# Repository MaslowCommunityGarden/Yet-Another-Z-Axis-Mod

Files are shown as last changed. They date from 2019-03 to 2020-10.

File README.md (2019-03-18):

# Yet Another Z-Axis Mod

I had gotten the z-axis kit with my Maslow originally, but I frequently found it off of spec when cutting. I tried all the simple fixes (bungee cord, gluing a bushing to the frame to keep alignment), and while they helped, I still had trouble with incomplete cuts way too often.

So I designed my own Z-axis kit that extends the stock solution, but doesn't rely on the Ridgid router's collar and it's not-intended-for-this-purpose mechanics.

The kit relies on the Z-axis motor from the original Maslow z-axis kit. Other than that all parts are 3D printed or listed in the BOM.
 
Additionally you will need the 3D printed parts from the forum and all the materials listed in the BOM.

Shout out to Gary D (@gder) for doing a **lot** of work beta testing and for contributing a bunch of ideas to the design. Thanks to Gary the design is a lot better than it would have been.

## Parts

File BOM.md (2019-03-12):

## Bill of Materials (BOM)

* Wood for the sled. 
* Linear Motion kit (or equivalent). You'll either need a linear-rod kit like <a href="https://smile.amazon.com/gp/product/B0797Q2C92">this one.</a> or equivalent parts. If you decide to source the parts yourself instead, here's what you really need from that kit:
	* 2x 8mm x 150mm smooth rails
	* 1x 8mm x 150mm lead screw
	* 4x LM 8UU bearings (the kit has these embedded inside linear slide blocks, but they pop out easily if you remove the retaining clip)
	* 1x 8mm lead-screw nut
	* 2x 42x24x10mm 8mm rail support block
	* 1x 48x12x27mm 8mm pillow block bearing
	* (You do not need the shaft couplers, plus there is an extra pillow block, and 2 extra rail support blocks)
* One 6mm to 8mm shaft coupler, like <a href="https://smile.amazon.com/gp/product/B06X9W3TNS">this one.</a>
* An assortment of <a href="https://smile.amazon.com/Stainless-Assortment-Precise-Beautiful-Printed/dp/B0714FLXND">M3 screws & nuts.
* Additionally you will need 4 M3x25mm screws
* You will also need some square M3 nuts, as well as some M6 and M8 ones. Probably best to get a kit like <a href="https://smile.amazon.com/gp/product/B06Y3NBT4Z">this one</a>.
* 4x M8 x 30mm hex screws (<a href="https://smile.amazon.com/Machine-Phillips-Threaded-M8-1-25-Threads/dp/B00917MQC8">phillips head</a> or <a href="https://smile.amazon.com/M8-1-25-Socket-Screws-Stainless-Machine/dp/B07GCMGP8S">"button" style</a> [that accepts a hex driver]).
* 2x M8 x 35mm hex screws
* 6x M6 x 35mm (up to 50mm) screws for the motor-assembly cross-braces
* Some M6 x 20mm screws and nuts and M5 x 15mm screws with nuts for mounting parts to the sled
* (Note: I got all of the M8/M6/M5 screws I needed by buying a TV mounting kit like <a href="https://smile.amazon.com/gp/product/B073WKR1QR/ref=oh_aui_search_asin_title?ie=UTF8&psc=1">this one</a>.)

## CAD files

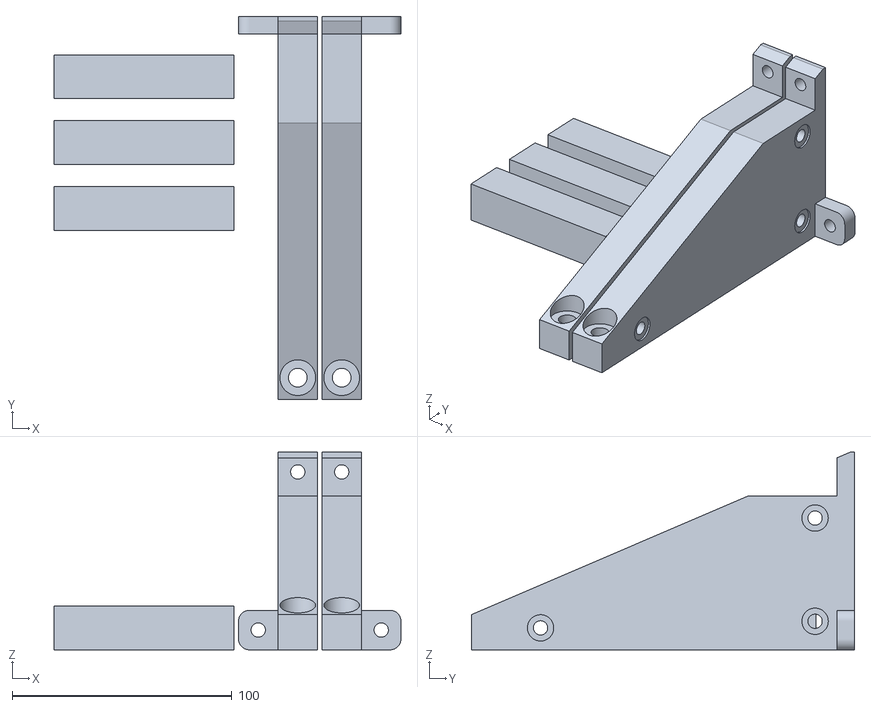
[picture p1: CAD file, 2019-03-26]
Project Files/v3_motor_brace_assembly_all.stl
158.0 x 174.5 x 90.0

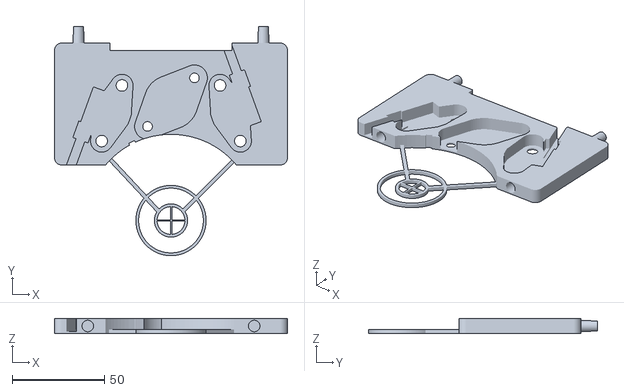
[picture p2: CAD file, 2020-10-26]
Project Files/individual parts (print only if needed)/v3_rods_base_alternate(for larger pillow-block).stl
126.0 x 124.0 x 8.00

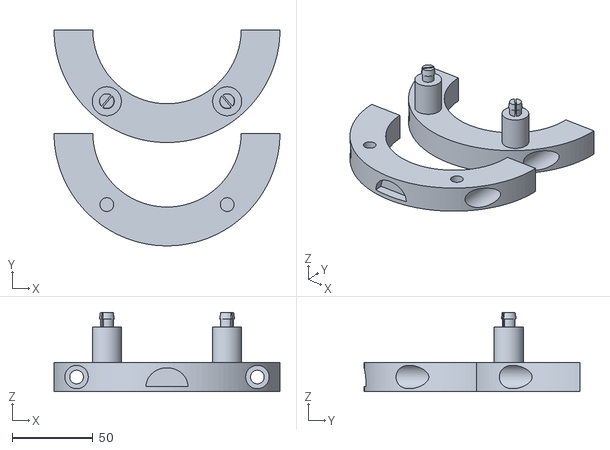
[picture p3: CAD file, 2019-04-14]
Project Files/v3_body_clamp_front_half_braced_pair.stl
140.0 x 133.6 x 49.0

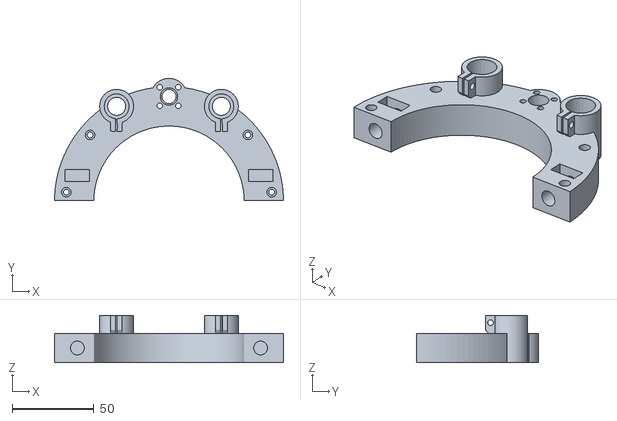
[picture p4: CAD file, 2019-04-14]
Project Files/individual parts (print only if needed)/v3_body_clamp_back_half_bottom_only.stl
140.0 x 74.7 x 29.0

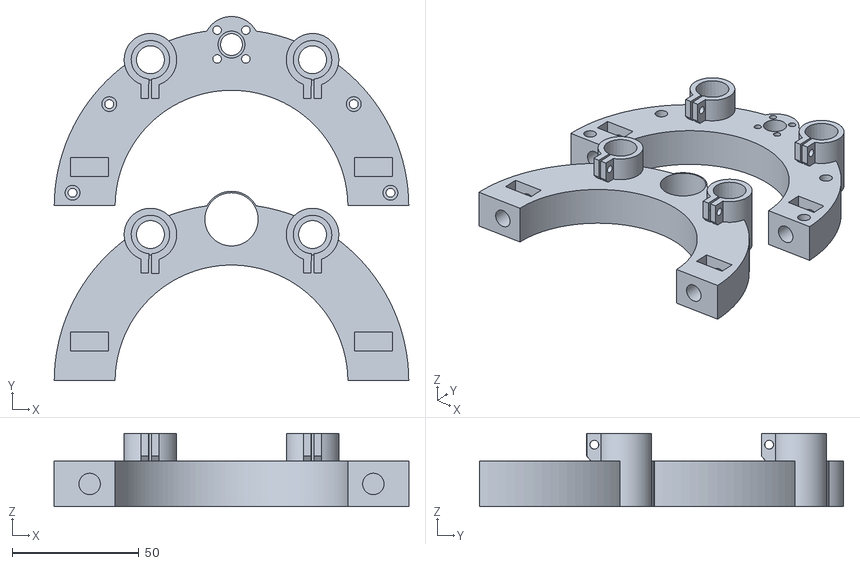
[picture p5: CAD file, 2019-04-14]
Project Files/v3_body_clamp_back_half_pair.stl
140.0 x 143.7 x 29.0

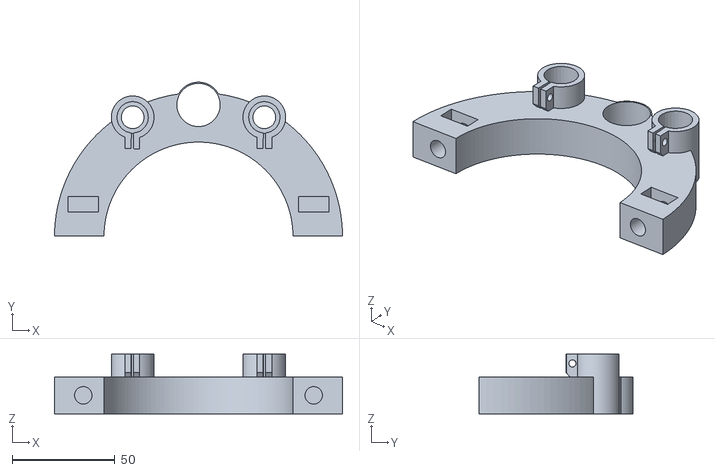
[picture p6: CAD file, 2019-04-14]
Project Files/individual parts (print only if needed)/v3_body_clamp_back_half_top_only.stl
140.0 x 74.7 x 29.0

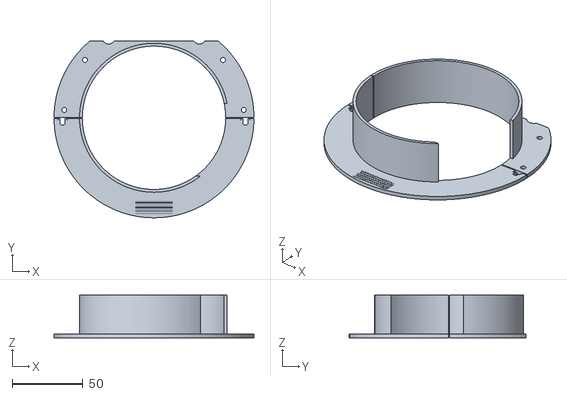
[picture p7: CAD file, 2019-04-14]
Project Files/individual parts (print only if needed)/v3_dust_sleeve_alternate_version.stl
141.0 x 124.5 x 30.0

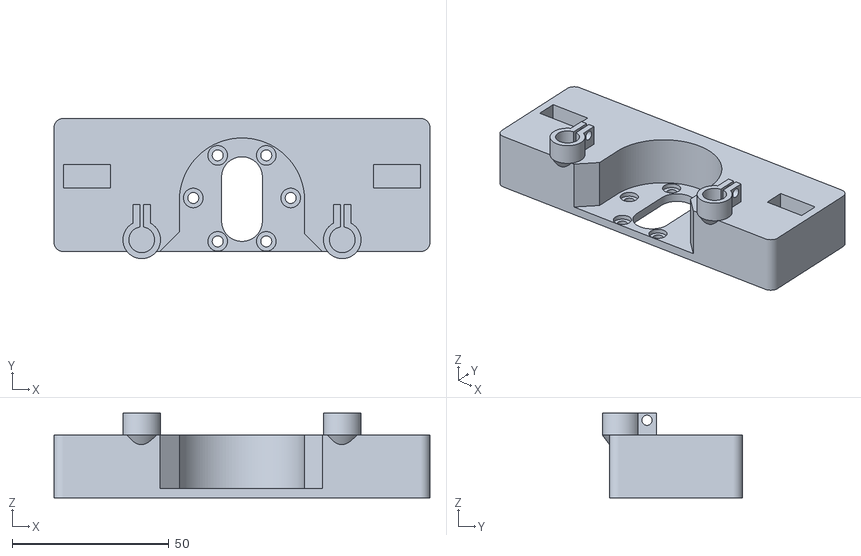
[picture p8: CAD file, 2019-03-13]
Project Files/v3_axis_cap.stl
120.0 x 44.8 x 27.0

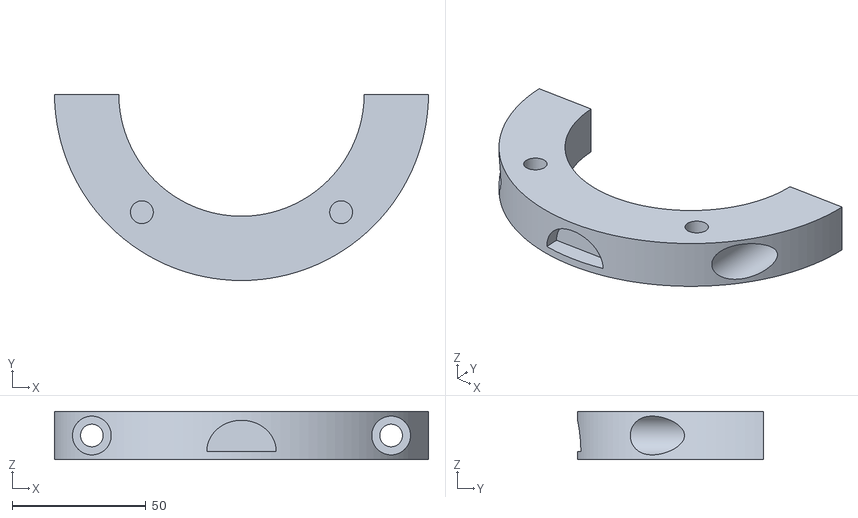
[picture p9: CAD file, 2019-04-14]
Project Files/individual parts (print only if needed)/v3_body_clamp_front_half_braced_pair_bottom_only.stl
140.0 x 69.6 x 18.0

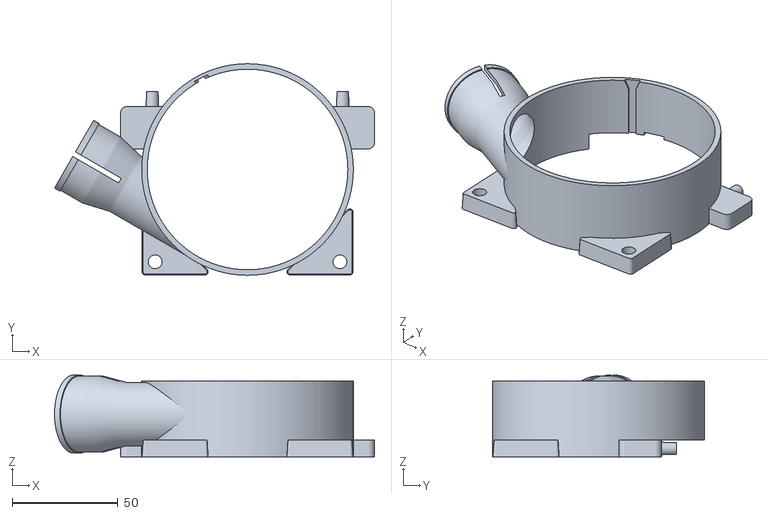
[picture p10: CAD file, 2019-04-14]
Project Files/individual parts (print only if needed)/v3_dust_shroud_alternate_version.stl
151.2 x 100.0 x 38.7

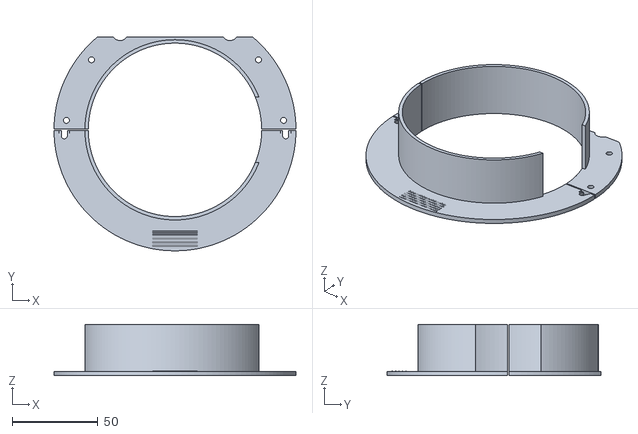
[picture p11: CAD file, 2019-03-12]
Project Files/v3_dust_sleeve.stl
141.0 x 124.5 x 30.0

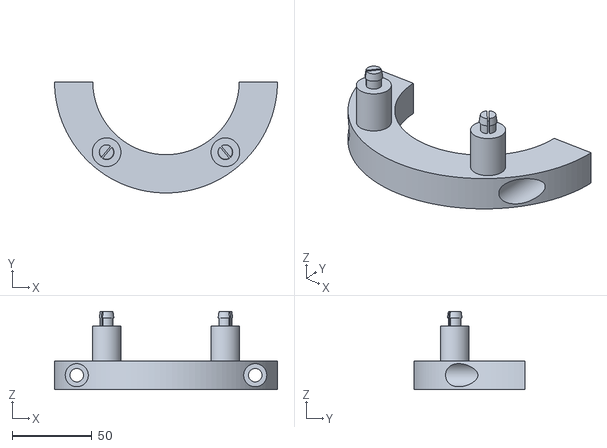
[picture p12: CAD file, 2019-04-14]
Project Files/individual parts (print only if needed)/v3_body_clamp_front_half_braced_pair_top_only.stl
140.0 x 69.6 x 49.0

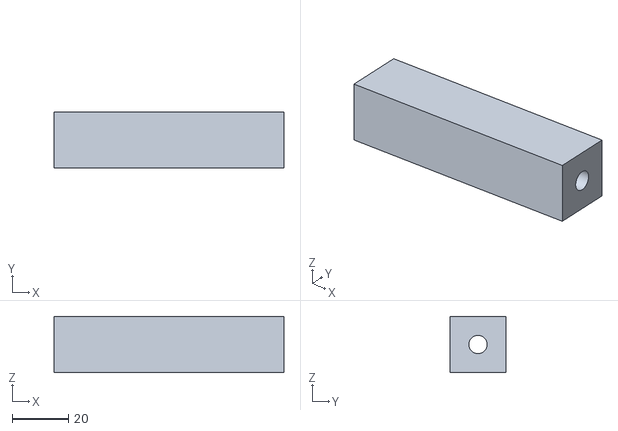
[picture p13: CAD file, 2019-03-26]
Project Files/individual parts (print only if needed)/motor_brace_cross_member.stl
82.0 x 20.0 x 20.0

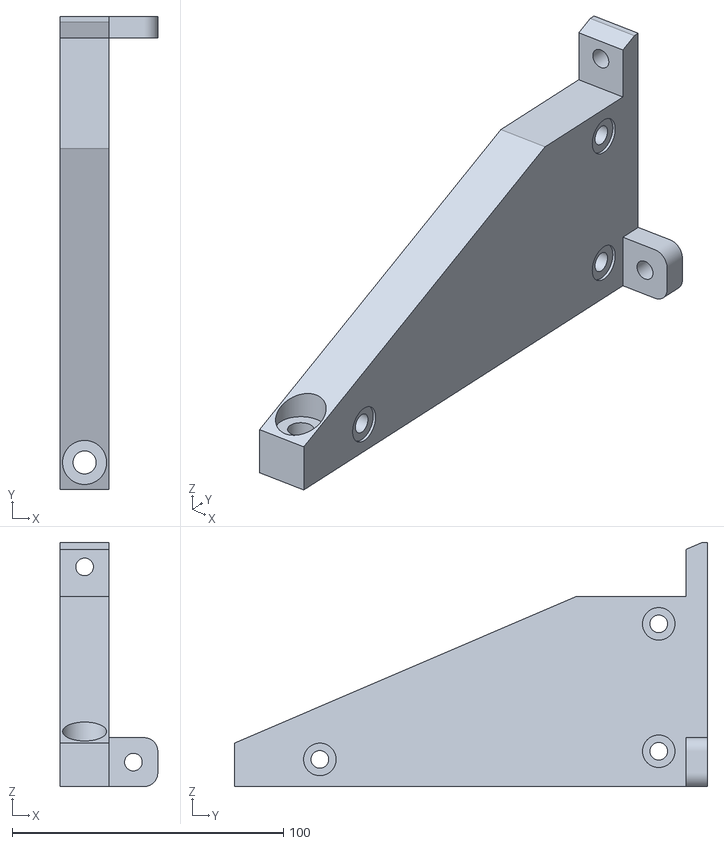
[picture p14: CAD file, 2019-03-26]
Project Files/individual parts (print only if needed)/motor_brace_left.stl
36.0 x 174.5 x 90.0

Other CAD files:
Project Files/v3_rods_base.stl
Project Files/individual parts (print only if needed)/motor_brace_both_left_and_right.stl
Project Files/individual parts (print only if needed)/motor_brace_right.stl

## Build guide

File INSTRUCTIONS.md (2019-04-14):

## Assembly

(**IMPORTANT NOTE**: There are now two alternate versions of the dust shroud and dust sleeve. If you have the ring kit or the original "L" brackets as your linkage system, then print the "standard" dust shroud and dust sleeve, which you will find in the main "Project Files" folder (v3_dust_shroud (use supports).stl and v3_dust_sleeve.stl). If you have a triangulation linkage kit (e.g. https://www.etsy.com/listing/558743441/maslow-triangulation-linkage-kit), you may need the alternate versions of the dust shroud (v3_dust_shroud_alternate_version.stl) and dust sleeve (v3_dust_sleeve_alternate_version.stl). You'll find those parts in the "Individual Parts" sub-folder. Please be sure to plan out where your linkage system attaches and then decide which version you need before you start printing, as it takes upwards of 6 hours to print those models out.)

(**NOTE**: These instructions are available to download at https://github.com/MaslowCommunityGarden/Yet-Another-Z-Axis-Mod/raw/master/Build%20Instructions.pdf. Github is not honoring all of my markdown around bullets, so the online instructions are formatted a bit funky.)

1. Print one set of all 3D printed parts. Where you need multiples of any given part, the provided STL files include the correct number of parts already. Some notes:
    1. PETG, ABS, or PLA should all be fine. I used PETG for mine.
    2. Default infill should be 20-25% or so, EXCEPT for the router body clamps (v3_body_clamp_back_half_pair.stl & v3_body_clamp_front_half_braced_pair.stl). Print those with at least 50% infill for clamping strength.
    3. You should not require supports on any parts EXCEPT the dust shroud (v3_dust_shroud (use supports).stl). Supports will be necessary unless you have a very dialed-in printer.
    4. Some post-printing cleanup may be required, especially on:
        * The slots where M3 square nuts slide in
        * The alignment pegs at the bottom of the rods base (v3_rods_base.stl) and the dust shroud (v3_dust_shroud (use supports).stl)
1. Cut a sled blank. I cut mine on a table saw out of some scrap plywood; just find a way to cut a ~17" roughly-circular blank. 
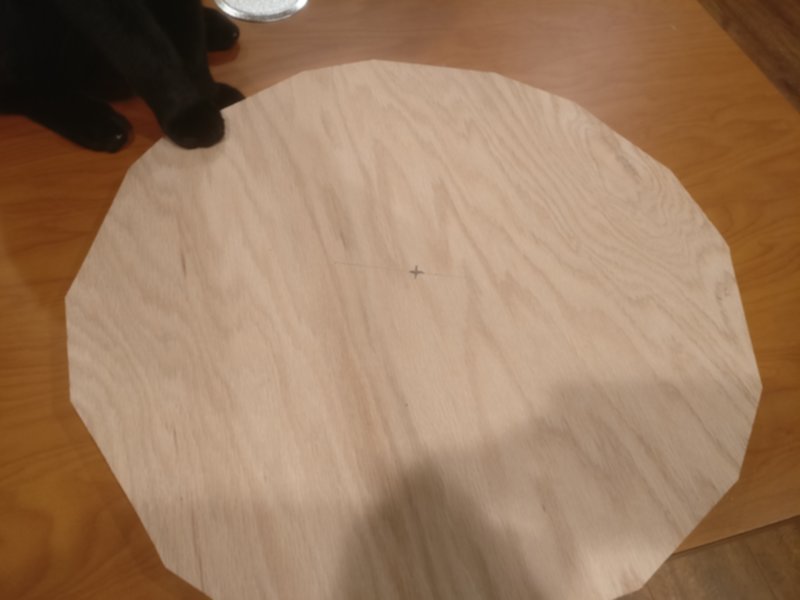
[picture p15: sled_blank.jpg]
Sled Blank
0. 
2. Mark the center on your sled blank and cut a 2 - 2.5" hole as close to center as possible.
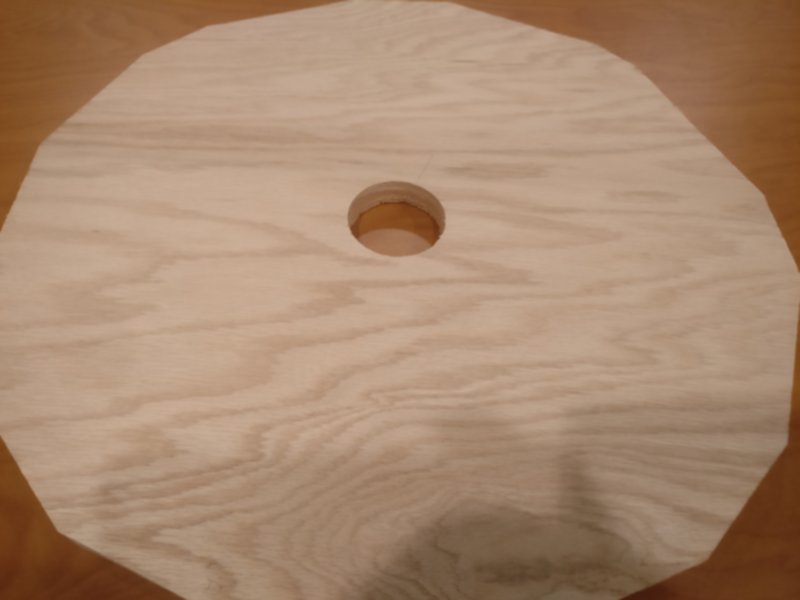
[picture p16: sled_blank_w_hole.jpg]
Sled Blank with Hole
0. 
1. Find the "rods base" (v3_rods_base.stl) in your 3D printed part set and position it so the snap-off "bullseye" is centered on the hole you just cut. 
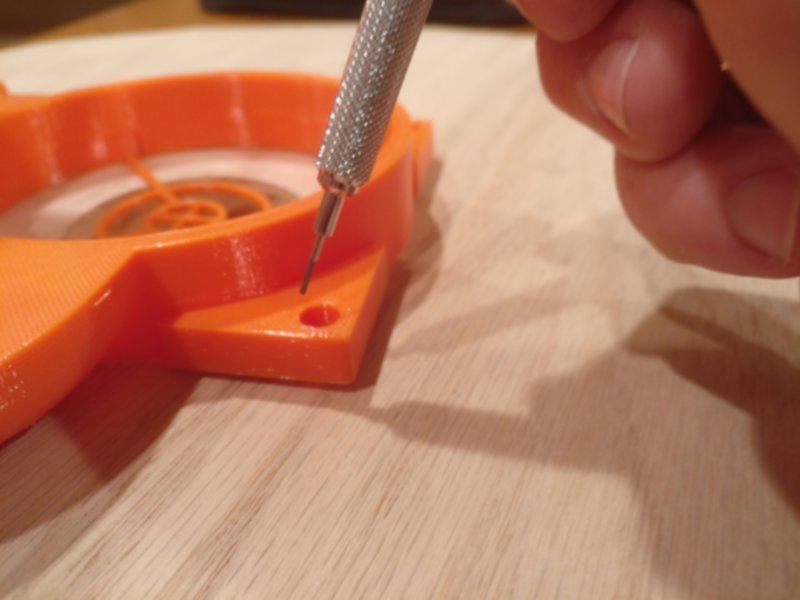
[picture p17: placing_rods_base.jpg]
Placing Rods Base
0. 
0. (**NOTE:** You can proceed to mark all the holes at one time and then drill them in a following step, or you can mark-drill, mark-drill. The latter is probably more accurate, but I did all my marking in one step, so that's how I talk it through here.)
0. Dry-fit the dust shroud (v3_dust_shroud (use supports).stl) to the rods base using the alignment pegs at the base. (Note, make sure you've cleaned up the pegs of any printing artifacts so you get a nice snug fit; if the pegs don't slide in all the way clean them up some more.)
0. Assemble all parts of the motor brace assembly (v3_motor_brace_assembly_all.stl). It should be self-explanatory enough how to assemble, and the result should look like the following photos. Just remember that you'll need 6 M6 bolts (35mm long to 50mm long) and 6 M6 square nuts to attach the cross-members.
0. Dry-fit the motor brace assembly to the rods  base (there are two alignment pegs at the base to ensure alignment. Remember to clean the pegs & holes up for a snug fit if needed.)
0. Now that you have all the parts that mount directly to the sled dry-fit, confirm the placement of the bullseye and mark all of the holes for drilling. Note:
    2. There are six holes in the rods base
    1. There are four holes in the motor brace assembly
    0. There are two holes in the dust shroud
    0. If you don't have another way to countersink, you can turn your router back into a hand-held router temporarily and use it to router out the countersink holes you need.
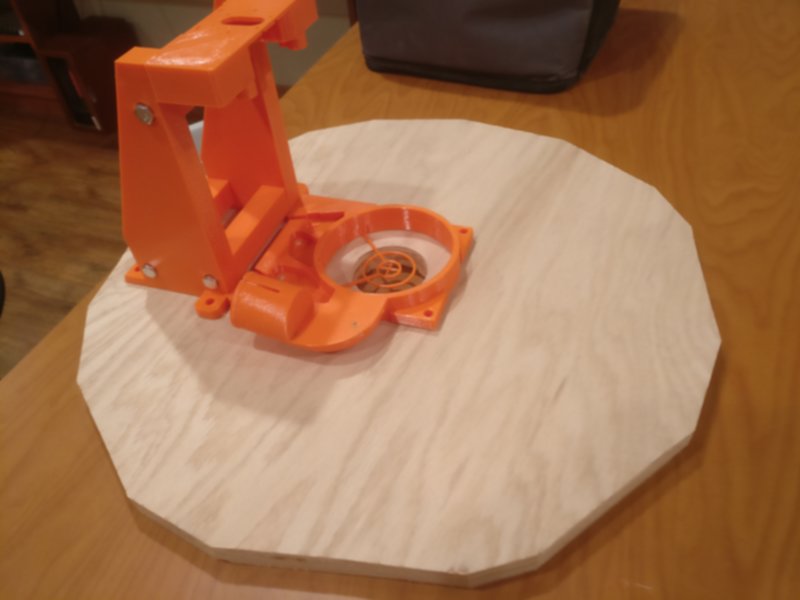
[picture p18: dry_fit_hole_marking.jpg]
Dry-fit / Hole Marking
0. 
0. Drill and countersink (from below) all the holes you marked.
0. Once you've drilled all of your holes, you can remove the bullseye from the rods base. Just use an X-acto knife or similar to snip it off close to the base:
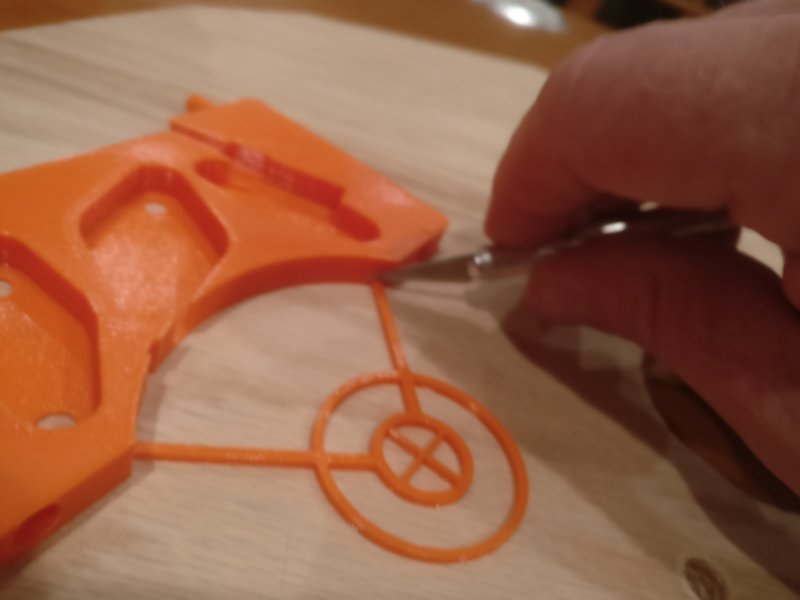
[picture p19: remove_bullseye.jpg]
Remove the Bullseye
    0. 
2. Now mount the two rail support blocks (left and right sides) and the pillow block (center) in the rods base and tighten them down fully. Some notes:
    0. Make sure to come up from below with your bolts.
    0. The pillow-block (center) uses M5 bolts. The rail support blocks take M6 bolts.
    0. The rail support blocks have a slot that is there to make it easier to tighten the lock screw. 
2. Mount the lead screw in the pillow block (in center). It uses two set screws to hold the lead screw fast.  (Note: on mine, the lead screw has a little wobble even when properly secured. It'll all firm up when it's fully assembled.)
3. Mount the linear rails in the rail support blocks and tighten the set screws.
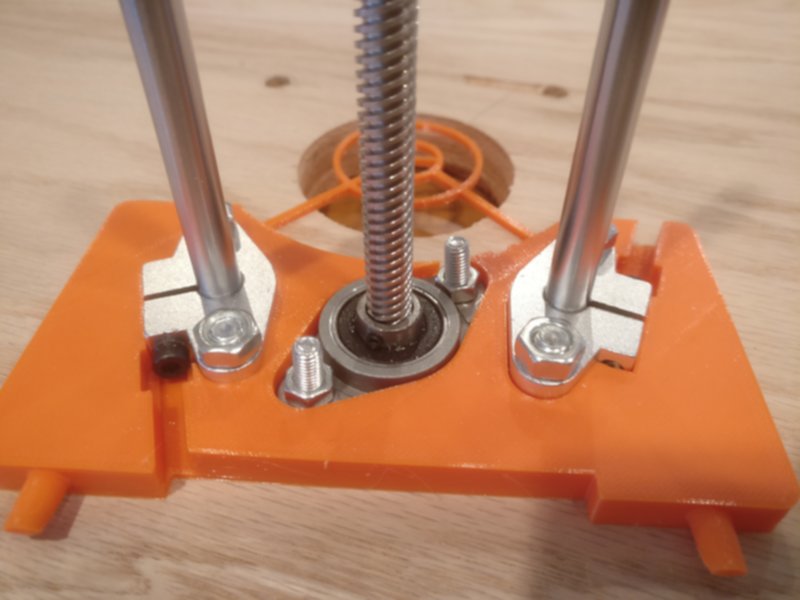
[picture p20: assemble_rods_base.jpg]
Assemble Rods Base
0. 
0. Now add the motor brace assembly and bolt it down fully from below.
0. Ditto the dust shroud. It should look like this when partially assembled:
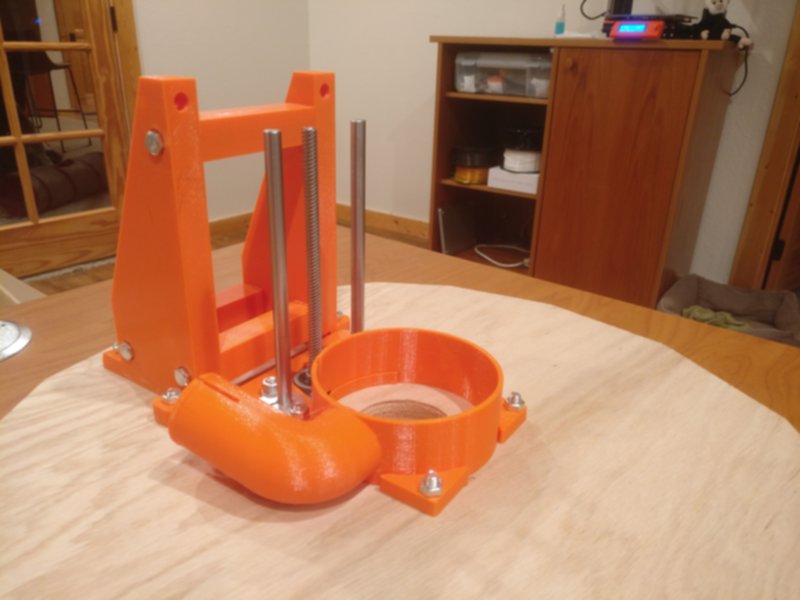
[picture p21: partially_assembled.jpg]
Partially Assembled
0. 
0. Now prepare the router clamp as follows:
    0. There are four parts to the router clamp, two per STL file (v3_body_clamp_back_half_pair.stl &amp; v3_body_clamp_front_half_braced_pair.stl).
    0. The two parts of the "lower half" join together with the cylindrical pegs, one to the other. Join them together now. (They will probably never come apart once joined, but if you want to be extra safe, put some CA glue in the holes before you join them.) (Note: ignore that in the photo both halves have that smiley-face cutout; yours will only have that on the "bottom" piece.)
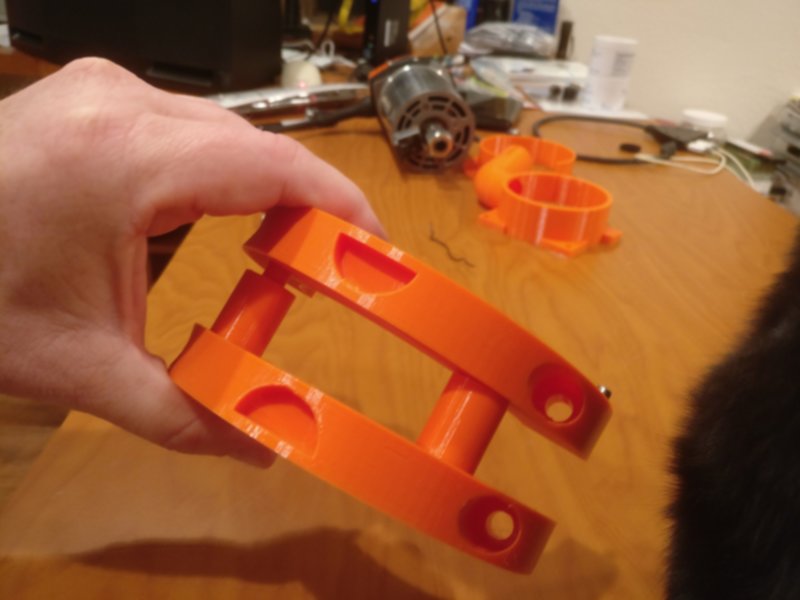
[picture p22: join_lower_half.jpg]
Join Lower Half
    0. 
    0. The two parts of the "upper" half don't physically join, but you will install them bearing-holder to bearing-holder.
    0. Insert the four 8UU bearings in the bearing holders in the "upper" halves and tighten down with M3x8mm screws and square nuts.
    0. Insert the lead-screw trapezoidal nut in the *bottom* piece of the "upper" half (the one with four additional M3 holes in it for bolting on the dust sleeve). This requires 4 M3x25mm screws and nuts.
    0. Use four M3x20mm screws and nuts to bolt the top half of the dust sleeve onto the bottom of the upper-half bottom:
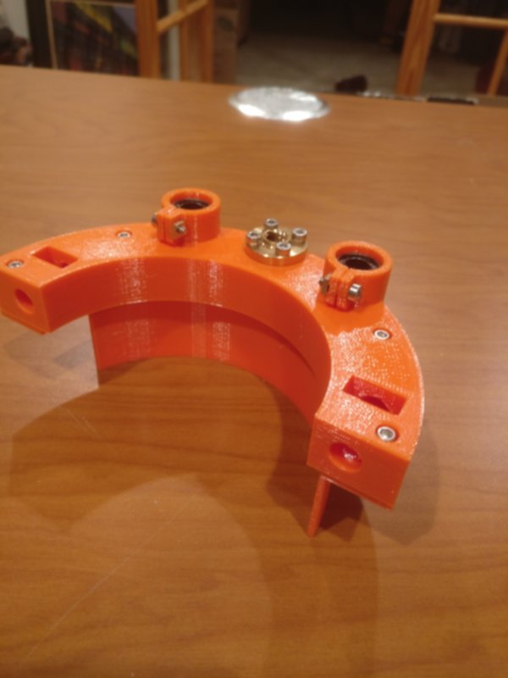
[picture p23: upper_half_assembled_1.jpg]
Upper Half Assembled (1)
    0. 
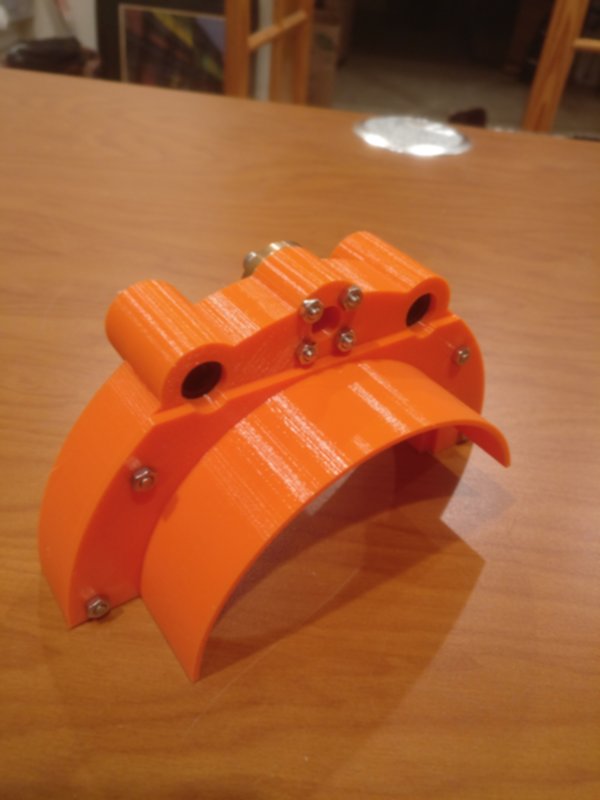
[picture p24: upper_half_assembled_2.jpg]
Upper Half Assembled (2)
    0. 
    0. Finally, insert two M3 square nuts in the bottom piece of the lower-half and place two 8mm M3 screws in them. There are two slots on the ends of the bottom piece to accept the nuts. (Note they will not screw all the way in; they are designed to stick out about 2 mm or so for cleating the dust sleeve.)
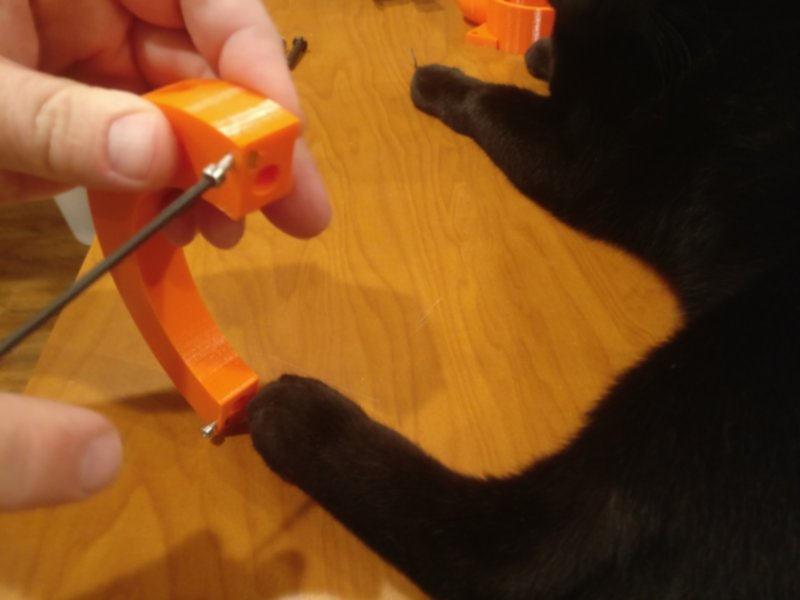
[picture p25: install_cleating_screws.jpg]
Install Cleating Screws
    0. 
    0. It's best if you try to get the cleating screws at about the right depth now; to do that, fit the bottom half of the dust sleeve (v3_dust_sleeve.stl) on the bottom of the clamp piece, and screw the screw in snugly, then **back it off 1/2 turn**. Now remove the dust sleeve, it goes on only when operating the rig.
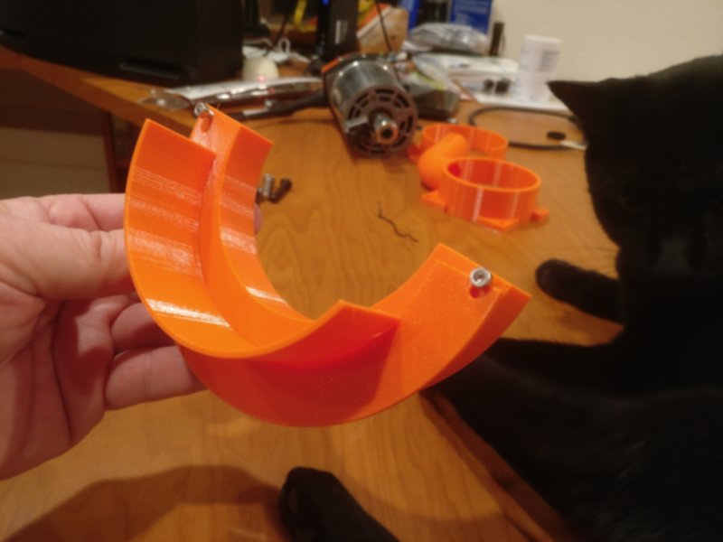
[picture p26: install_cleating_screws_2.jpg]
Install Cleating Screws (2)
    0. 
0. Install the upper half of the router clamp:
    0. Place the "bottom" piece (the one with the dust sleeve attached) on the rails. Some notes:
        a. Be gentle, if you come in at too much of an angle, you can force ball bearings out of your linear bearing.
        a. You might have to gently straighten out the tops of the linear rods to seat the bearings correctly.
        a. Once you have the bearings on, you will need to push down a little to get the trapezoidal nut to engage the lead screw.
        a. Once the lead screw is engaged, you can move the clamp up and down by turning the lead screw manually.
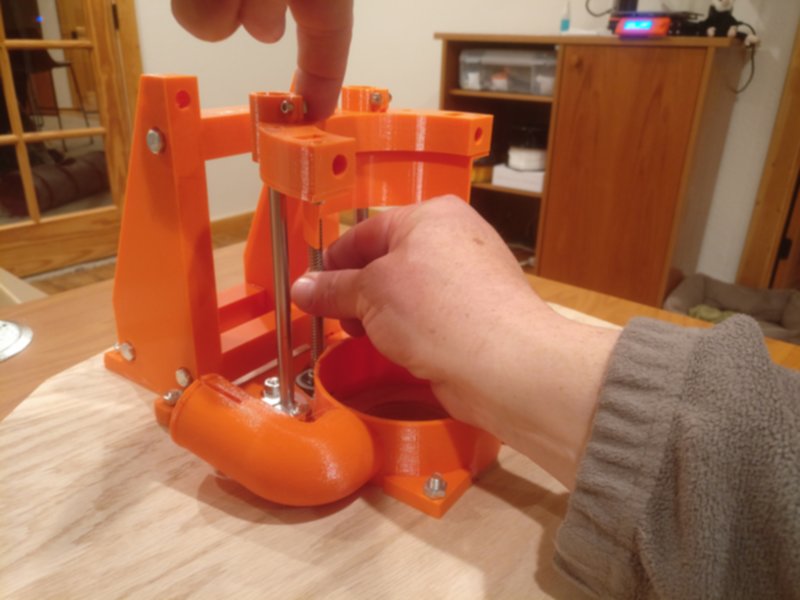
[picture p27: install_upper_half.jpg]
Install Upper Half
        a. 
        a. Now place the other top-half piece, making sure to flip it so the bearing holders are touching each other, as shown.
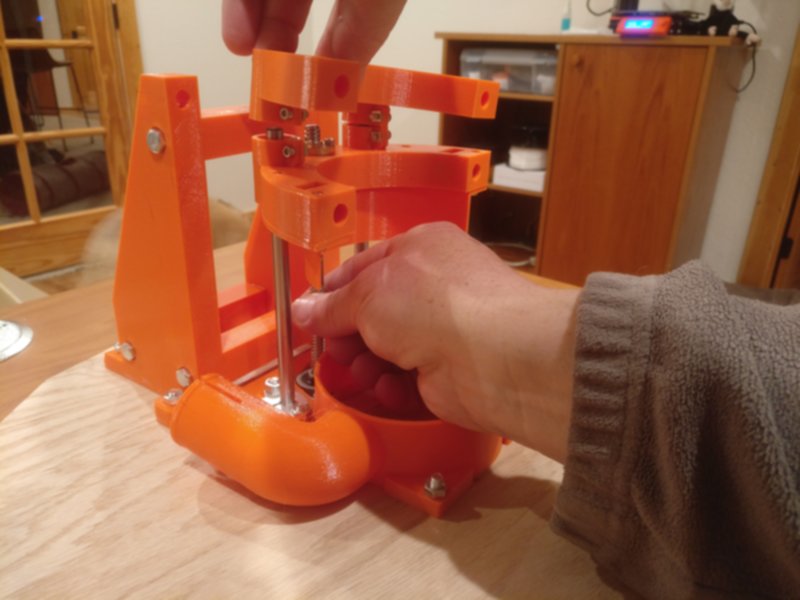
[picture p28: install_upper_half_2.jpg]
Install Upper Half (2)
        a. 
0. Assemble the Axis Cap:
    0. Find the 3D printed part for the Axis Cap (v3_axis_cap.stl)
    0. Insert two M3x8mm screws and *square nuts* in the rod holders. (If you don't use square nuts, you will have to hold the nuts with needlenose pliers when tightening them.) **Leave these loose / not fully tightened.**
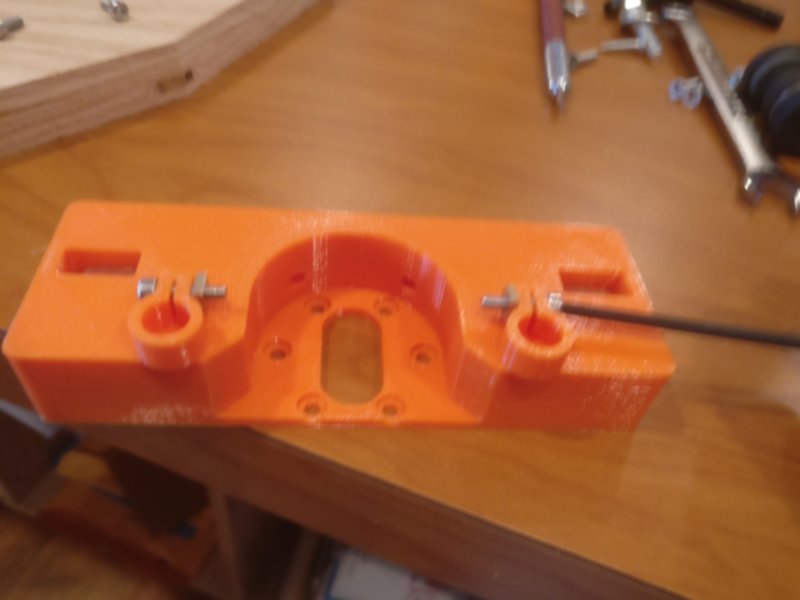
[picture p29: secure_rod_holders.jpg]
Rod Holders
    0. 
    0. You do not need to install square nuts in the slots in the top of the axis cap; that's a remnant of a previous design iteration.
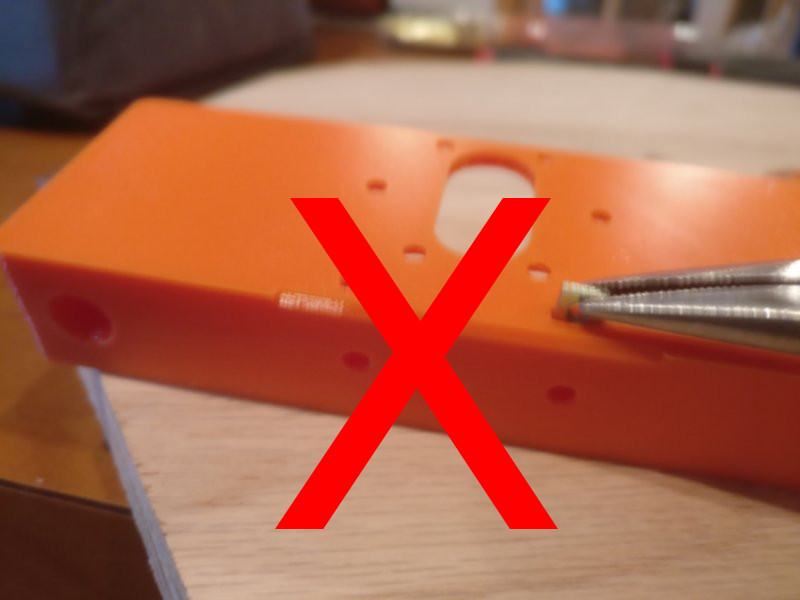
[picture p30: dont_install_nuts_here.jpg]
Don't Install Square Nuts
    0. 
    0. Now use 6 M3x6mm screws to mount the motor from your stock kit. Note the motor shaft should be towards the open side of the axis cap, as shown:
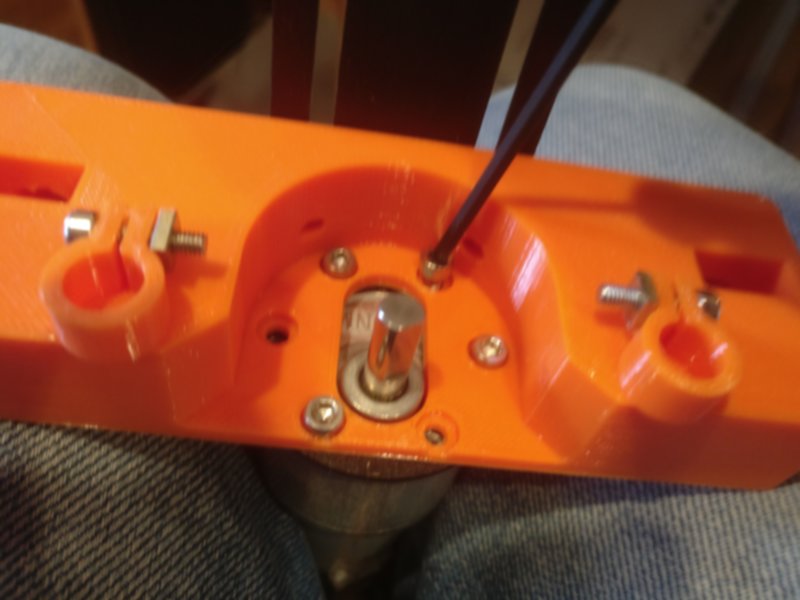
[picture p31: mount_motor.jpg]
Mount Motor in Axis Cap
    0. 
0. Mount the Axis Cap:
    0. Find your coupler (from the BOM, not from the stock kit) and slide it on the lead screw. Do not tighten yet.
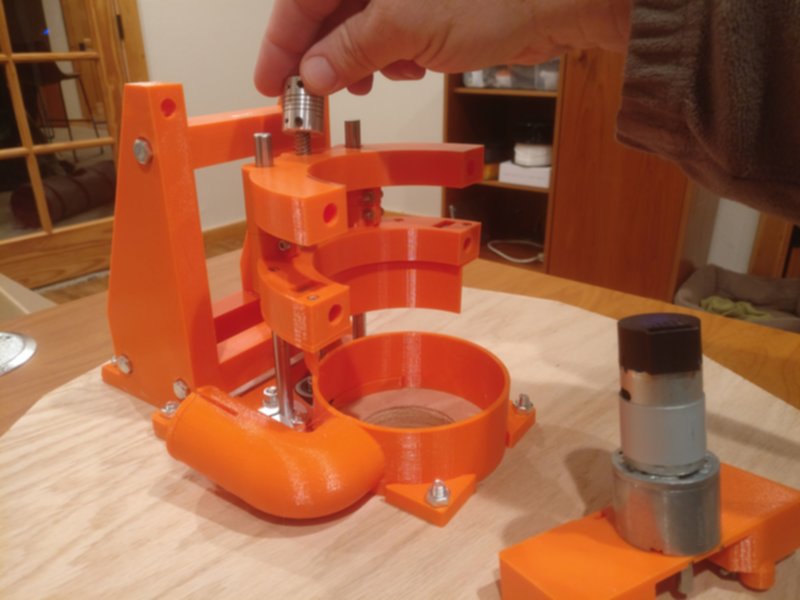
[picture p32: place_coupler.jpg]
Place Coupler
    0. 
    0. Gently place the axis cap on top of the linear rails and slide the motor shaft into the coupler, as shown:
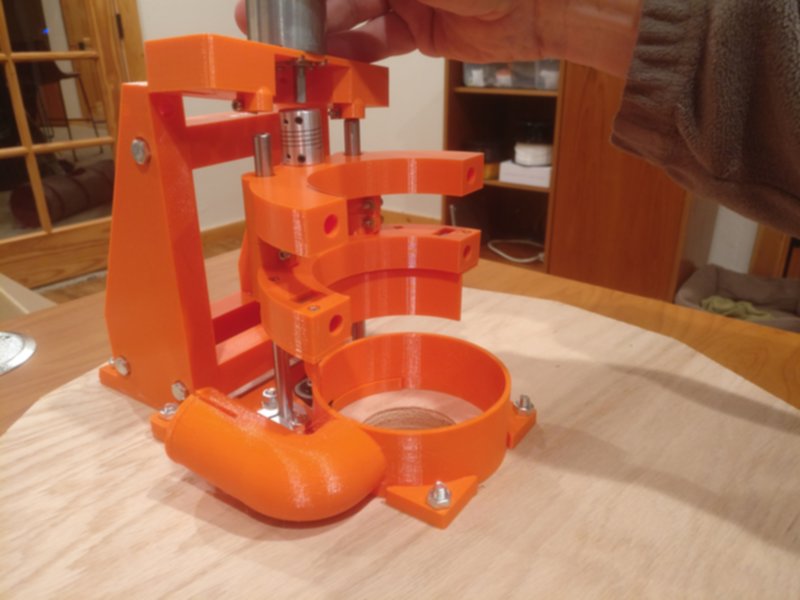
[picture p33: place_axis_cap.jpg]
Place Axis Cap
    0. 
    0. Now attach the coupler onto the motor shaft and lead screw using the set screws. Some notes on this:
        0. Slide the coupler up a bit to preserve your full range of motion. But not so high it will grind against the motor screws when in operation.
        0. The upper set screw tightens against the flat side of the motor shaft.
        0. You may need to connect your motor to GroundControl (GC) to get the shaft oriented so you can access the flat side. Use small moves to get the shaft in the correct position.
        0. Once you have the coupler fixed to the motor, use the lower set screw to clamp it to the lead screw.
        0. Following this, find the *other* two set screws and tighten them down as well; this will make sure everything is tight and secure. (Again, you may need to use GC to orient the shaft to permit you access.)
        0. Finally, tighten those M3 screws that secure the linear rods into the rod holders underneath the axis cap.
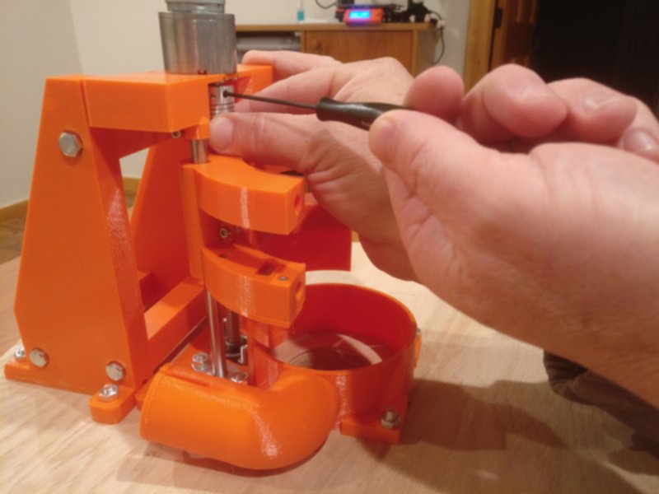
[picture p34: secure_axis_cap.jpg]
Secure Axis Cap
    0. 
0. Bolt the Axis Cap to the Motor Brace Assembly using two 8Mx35mm bolts and two M8 square nuts. You will need to hold the square nuts in place from underneath--the slots for them are on the bottom face of the Axis Cap.
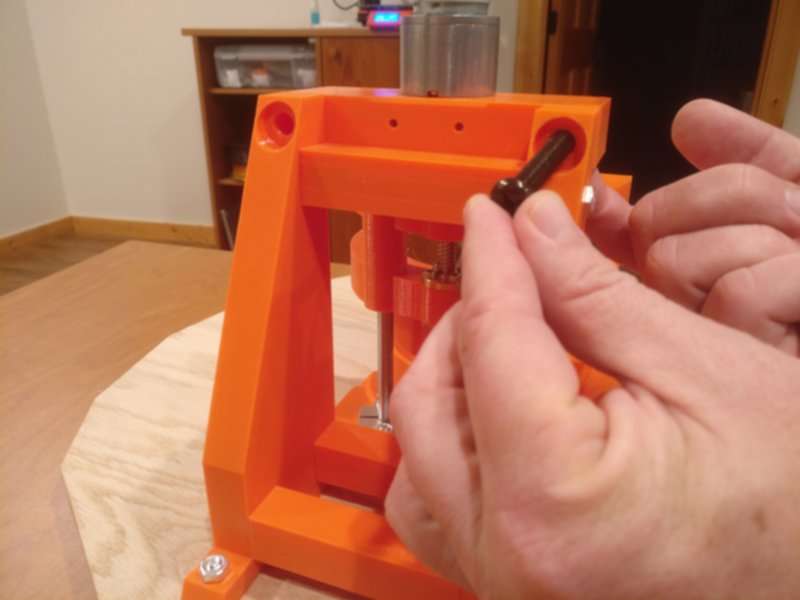
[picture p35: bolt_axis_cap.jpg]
Bolt Axis Cap
    0. 
0. Place the Router
    0. Now it's time to place the router. Lay it into the groove created by the two top-half clamps with the front of the router facing towards the hose coupler.
    0. If you had previously greased your router body, as is recommended for the stock kit, clean that grease off before placing it. We don't need it slipping inside the clamp.
    0. Leave about an inch or so of the router body visible below the bottom-most part of the clamp. (You can fine-tune the placement later if you find you have too much or too little vertical range.)
    0. The braced-pair "lower" half of the router clamp needs to be mounted to hold it in place. Be sure you place the lower half correctly: with the "smiley" hole and the cleat-screws closer to the sled.
    0. Use 4 M8x35mm bolts and M8 square nuts to secure the lower half of the clamp. It can be a bit tricky to place the nuts, hold the router, and screw things together. It's a bit easier if you flip the whole rig on its back on a table.
    0. It's not horribly important that you have your router precisely facing the hose opening, but get it as close to that as possible. If you mount it wrong, the power cord and back part of the router can make contact with the axis cap and cause runtime issues.
    0. Don't tighten the M8 bolts right away, just make them snug at first. Then check the router's placement and orientation and tighten things down.
    0. When tightening, alternate between the left-side and right-side bolts, using small (e.g. 1/4 turn) turns. This makes sure you don't stress one side of the clamp too much.
    0. Here's where you find out if you printed the router clamp with enough infill. Less than 50% infill and it's liable to crack when you try to tighten it down fully.
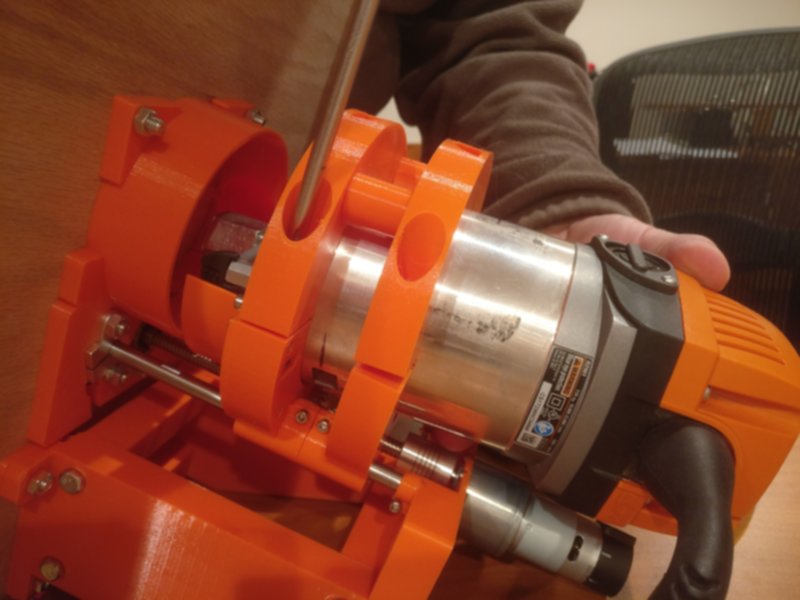
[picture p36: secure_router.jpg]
Secure Router
    0. 
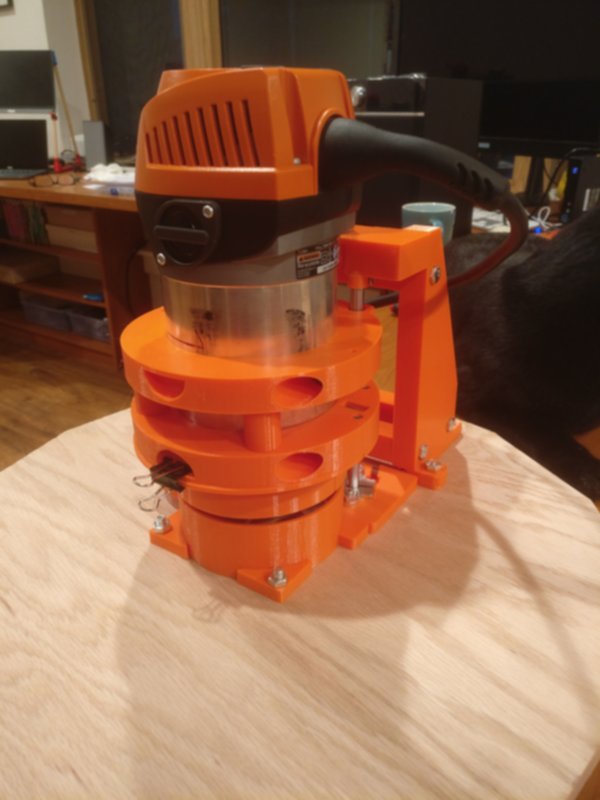
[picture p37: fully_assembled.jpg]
Fully Assembled


### Pre-flight and Usage

0. Before attempting any moves in GC, be sure to modify your GC configuration. Find the setting for Z-axis pitch, and put the appropriate setting for your lead screw. If you bought the kit I linked in the BOM, that value should be 8mm.
    0. NOTE that this kit does not have an end-stop, so you can tell GC to crash the nut into the coupler or the pillow-block at bottom. Be cautious in your moves, and be ready to hit the "Stop!" button in GC if you've mistakenly told GC to lower / raise beyond the limits.
    0. Test your kit by moving your new z axis up and down (in small increments at first).
    0. Prior to actually doing any cutting, be sure to define "zero" on your newly-installed Z axis kit.
0. The dust sleeve is designed to go on and come off easily so you can access the collet and change bits. To place it initially:
    0. Slide the back into the cleating screws you placed in the bottom of the body clamp:
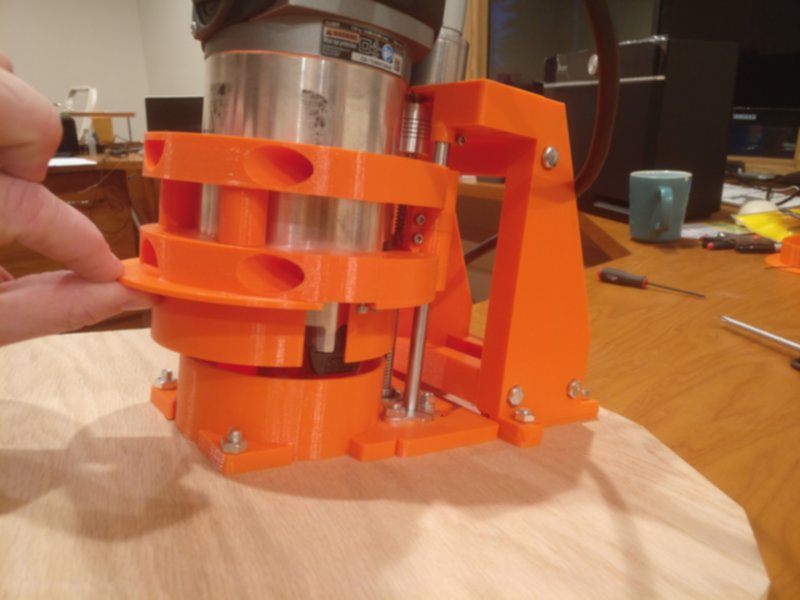
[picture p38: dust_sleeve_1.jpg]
Using the Dust Sleeve
    0. 
    0. Once the sleeve is fully engaged on the cleating screws, place a medium-size binder clip at the front clip-point (the smiley-shaped opening):
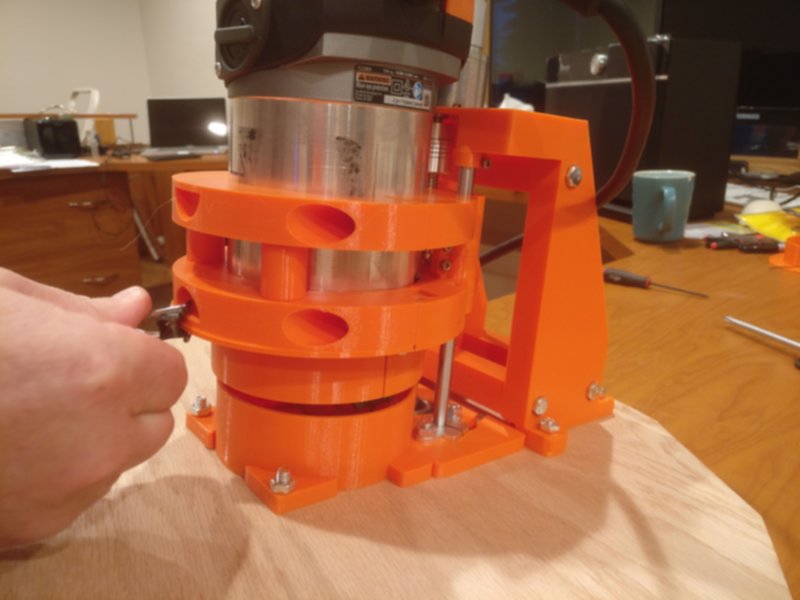
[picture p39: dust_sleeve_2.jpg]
Using the Dust Sleeve
    0. 
0. To access your collet and change bits and zero your router:
    0. Remove the binder clip and remove the front part of the dust sleeve
    0. Raise your router to maximum height so it clears the dust shroud
    0. You should be able to access the collet lock from behind, and get a wrench into the opening where the dust sleeve had been.

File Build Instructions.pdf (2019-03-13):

3/13/2019 | pandoc-temp-e5OjH4.html
file:///tmp/pandoc-temp-e5OjH4.html | 1/23

## Read.me

I had gotten the z-axis kit with my Maslow originally, but I frequently found it off of spec when cutting. I tried all the simple fixes (bungee cord, gluing a bushing to the frame to keep alignment), and while they helped, I still had trouble with incomplete cuts way too often.

So I designed my own Z-axis kit that extends the stock solution, but doesn't rely on the Ridgid router's collar and it's not-intended-for-this-purpose mechanics.

The kit relies on the Z-axis motor from the original Maslow z-axis kit. Other than that all parts are 3D printed or listed in the BOM.

Additionally you will need the 3D printed parts from the forum and all the materials listed in the BOM.

## Bill of Materials (BOM)

Wood for the sled.
Linear Motion kit (or equivalent). You'll either need a linear-rod kit like this one. (https://smile.amazon.com/gp/product/B0797Q2C92) or equivalent parts. If you decide to source the parts yourself instead, here's what you really need from that kit:
2x 8mm x 150mm smooth rails
1x 8mm x 150mm lead screw
4x LM 8UU bearings (the kit has these embedded inside linear slide blocks, but they pop out easily if you remove the retaining clip) 1x 8mm lead-screw nut
2x 42x24x10mm 8mm rail support block
1x 48x12x27mm 8mm pillow block bearing
(You do not need the shaft couplers, plus there is an extra pillow block, and 2 extra rail support blocks) One 6mm to 8mm shaft coupler, like this one. (https://smile.amazon.com/gp/product/B06X9W3TNS)
An assortment of M3 screws & nuts.
Additionally you will need 4 M3x25mm screws
You will also need some square M3 nuts, as well as some M6 and M8 ones. Probably best to get a kit like (https://smile.amazon.com/Stainless-Assortment-Precise-Beautiful-Printed/dp/B0714FLXND) this one. (https://smile.amazon.com/gp/product/B06Y3NBT4Z) 4x M8 x 30mm hex screws (phillips head (https://smile.amazon.com/Machine-Phillips-Threaded-M8-1-25-Threads/dp/B00917MQC8) or "button" style (https://smile.amazon.com/M8-1-25-Socket-Screws-Stainless-Machine/dp/B07GCMGP8S) [that accepts a hex driver]).
2x M8 x 35mm hex screws
6x M6 x 35mm (up to 50mm) screws for the motor-assembly cross-braces
Some M6 x 20mm screws and nuts and M5 x 15mm screws with nuts for mounting parts to the sled (Note: I got all of the M8/M6/M5 screws I needed by buying a TV mounting kit like this one.) (https://smile.amazon.com/gp/product/B073WKR1QR/ref=oh_aui_search_asin_title?ie=UTF8&psc=1)

## Assembly

1. Print one set of all 3D printed parts. Where you need multiples of any given part, the provided STL files include the correct number of parts already. Some notes:
1. PETG, ABS, or PLA should all be fine. I used PETG for mine.
2. Default infill should be 20-25% or so, EXCEPT for the router body clamps (v3_body_clamp_upper_half_pair.stl & v3_body_clamp_lower_half_braced_pair.stl). Print those with at least 50% infill for clamping strength.
3. You should not require supports on any parts EXCEPT the dust shroud (v3_dust_shroud (use supports).stl). Supports will be necessary unless you have a very dialed-in printer.
4. Some post-printing cleanup may be required, especially on:
The slots where M3 square nuts slide in
The alignment pegs at the bottom of the rods base (v3_rods_base.stl) and the dust shroud (v3_dust_shroud (use supports).stl)
2. Cut a sled blank. I cut mine on a table saw out of some scrap plywood; just find a way to cut a ~17" roughly-circular blank.

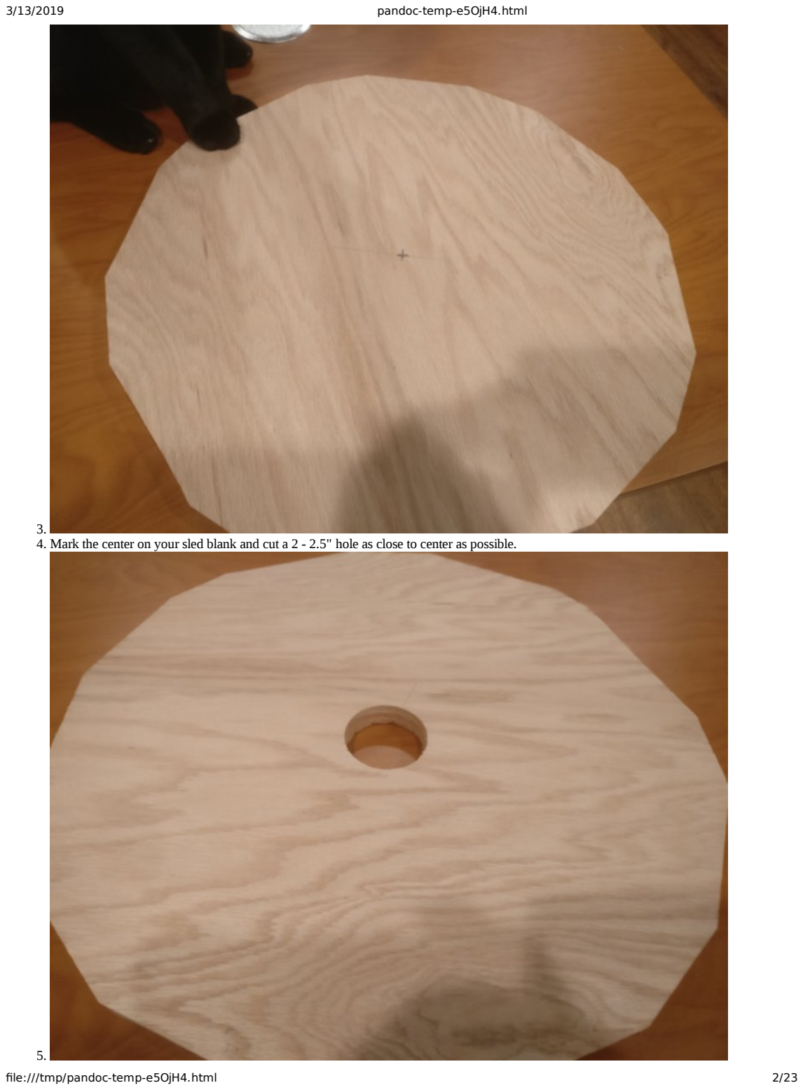
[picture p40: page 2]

3.
4. Mark the center on your sled blank and cut a 2 - 2.5" hole as close to center as possible.

5.

6. Find the "rods base" (v3_rods_base.stl) in your 3D printed part set and position it so the snap-off "bullseye" is centered on the hole you just cut.


7.
8. (NOTE: You can proceed to mark all the holes at one time and then drill them in a following step, or you can mark-drill, mark-drill. The latter is probably more accurate, but I did all my marking in one step, so that's how I talk it through here.)
9. Dry-fit the dust shroud (v3_dust_shroud (use supports).stl) to the rods base using the alignment pegs at the base. (Note, make sure you've cleaned up the pegs of any printing artifacts so you get a nice snug fit; if the pegs don't slide in all the way clean them up some more.)
10. Assemble all parts of the motor brace assembly (v3_motor_brace_assembly_all.stl). It should be self-explanatory enough how to assemble, and the result should look like the following photos. Just remember that you'll need 6 M6 bolts (35mm long to 50mm long) and 6 M6 square nuts to attach the cross-members.
11. Dry-fit the motor brace assembly to the rods base (there are two alignment pegs at the base to ensure alignment. Remember to clean the pegs & holes up for a snug fit if needed.)
12. Now that you have all the parts that mount directly to the sled dry-fit, confirm the placement of the bullseye and mark all of the holes for drilling. Note:
2. There are six holes in the rods base
3. There are four holes in the motor brace assembly
4. There are two holes in the dust shroud
5. If you don't have another way to countersink, you can turn your router back into a hand-held router temporarily and use it to router out the countersink holes you need.


13.
14. Drill (from above) and countersink (from below) all the holes you marked.
15. Once you've drilled all of your holes, you can remove the bullseye from the rods base. Just use an X-acto knife or similar to snip it off close to the base:


0.
16. Now mount the two rail support blocks (left and right sides) and the pillow block (center) in the rods base and tighten them down fully. Some notes:
0. Make sure to come up from below with your bolts.
1. The pillow-block (center) uses M5 bolts. The rail support blocks take M6 bolts.
2. The rail support blocks have a slot that is there to make it easier to tighten the lock screw.
17. Mount the lead screw in the pillow block (in center). It uses two set screws to hold the lead screw fast. (Note: on mine, the lead screw has a little wobble even when properly secured. It'll all firm up when it's fully assembled.)
18. Mount the linear rails in the rail support blocks and tighten the set screws.


19.
20. Now add the motor brace assembly and bolt it down fully from below.
21. Ditto the dust shroud. It should look like this when partially assembled:


22.
23. Now prepare the router clamp as follows:
0. There are four parts to the router clamp, two per STL file (v3_body_clamp_upper_half_pair.stl & v3_body_clamp_lower_half_braced_pair.stl).
1. The two parts of the "lower half" join together with the cylindrical pegs, one to the other. Join them together now. (They will probably never come apart once joined, but if you want to be extra safe, use some CA glue on the join pieces before you join them.) (Note: ignore that in the photo both halves have that smiley-face cutout; yours will only have that on the "bottom" piece.)


2.
3. The two parts of the "upper" half don't physically join, but you will install them bearing-holder to bearing-holder.
4. Insert the four 8UU bearings in the bearing holders in the "upper" halves and tighten down with M3x8mm screws and square nuts.
5. Insert the lead-screw trapezoidal nut in the bottom piece of the "upper" half (the one with four additional M3 holes in it for bolting on the dust sleeve). This requires 4 M3x25mm screws and nuts.
6. Use four M3x20mm screws and nuts to bolt the top half of the dust sleeve onto the bottom of the upper-half bottom:


7.


8.
9. Finally, insert two M3 square nuts in the bottom piece of the lower-half and place two 8mm M3 screws in them. There are two slots on the ends of the bottom piece to accept the nuts. (Note they will not screw all the way in; they are designed to stick out about 2 mm or so for cleating the dust sleeve.)


10.
11. It's best if you try to get the cleating screws at about the right depth now; to do that, fit the bottom half of the dust sleeve (v3_dust_sleeve.stl) on the bottom of the clamp piece, and screw the screw in snugly, then back it off 1/2 turn. Now remove the dust sleeve, it goes on only when operating the rig.


12.
24. Install the upper half of the router clamp:
0. Place the "bottom" piece (the one with the dust sleeve attached) on the rails. Some notes:
a. Be gentle, if you come in at too much of an angle, you can force ball bearings out of your linear bearing.
b. You might have to gently straighten out the tops of the linear rods to seat the bearings correctly.
c. Once you have the bearings on, you will need to push down a little to get the trapezoidal nut to engage the lead screw.
d. Once the lead screw is engaged, you can move the clamp up and down by turning the lead screw manually.

e.


f. Now place the other top-half piece, making sure to flip it so the bearing holders are touching each other, as shown.

g.


25. Assemble the Axis Cap:
0. Find the 3D printed part for the Axis Cap (v3_axis_cap.stl)
1. Insert two M3x8mm screws and square nuts in the rod holders. (If you don't use square nuts, you will have to hold the nuts with needlenose pliers when tightening them.) Leave these loose / not fully tightened.


2.
3. If your printed part has these holes, you do not need to install square nuts in the slots in the top of the axis cap; that's a remnant of a previous design iteration.


4.
5. Now use 6 M3x6mm screws to mount the motor from your stock kit. Note the motor shaft should be towards the open side of the axis cap, as shown:


6.
26. Mount the Axis Cap:
0. Find your coupler (from the BOM, not from the stock kit) and slide it on the lead screw. Do not tighten yet.

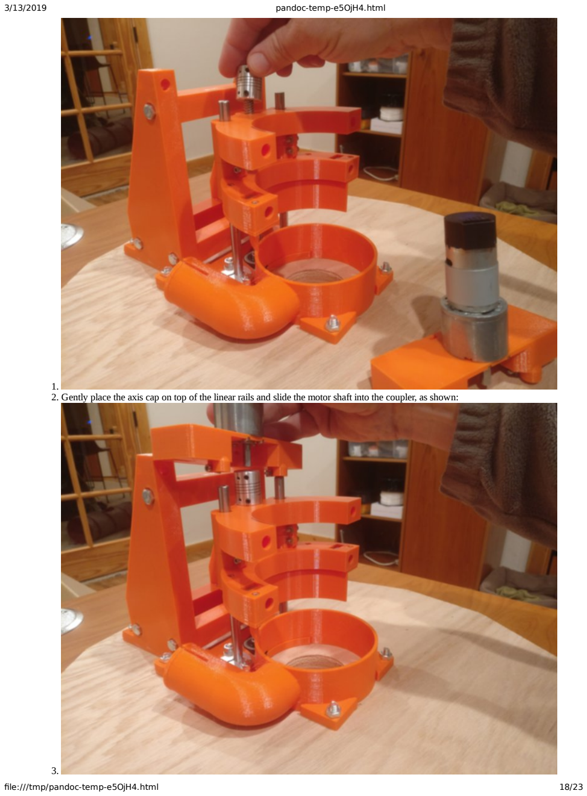
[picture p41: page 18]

1.
2. Gently place the axis cap on top of the linear rails and slide the motor shaft into the coupler, as shown:

3.

4. Now attach the coupler onto the motor shaft and lead screw using the set screws. Some notes on this:
0. Slide the coupler up a bit to preserve your full range of motion. But not so high it will grind against the motor screws when in operation.
1. The upper set screw tightens against the flat side of the motor shaft.
2. You may need to connect your motor to GroundControl (GC) to get the shaft oriented so you can access the flat side. Use small moves to get the shaft in the correct position.
3. Once you have the coupler fixed to the motor, use the lower set screw to clamp it to the lead screw.
4. Following this, find the other two set screws and tighten them down as well; this will make sure everything is tight and secure. (Again, you may need to use GC to orient the shaft to permit you access.)
5. Finally, tighten those M3 screws that secure the linear rods into the rod holders underneath the axis cap.


5.
27. Bolt the Axis Cap to the Motor Brace Assembly using two 8Mx35mm bolts and two M8 square nuts. You will need to hold the square nuts in place from underneath--the slots for them are on the bottom face of the Axis Cap.


0.
28. Place the Router
0. Now it's time to place the router. This is easiest if you lay the whole rig on its back (with the sled perpendicular to the floor).
1. If you had previously greased your router body, as is recommended for the stock kit, clean that grease off before placing it. We don't need it slipping inside the clamp.
2. Lay the router into the groove created by the two top-half clamps with the front of the router facing towards the hose coupler.
3. Leave about 3/4" or so of the router body visible below the bottom-most part of the clamp. (You can fine-tune the placement later if you find you have too much or too little vertical range.)
4. The braced-pair "lower" half of the router clamp needs to be mounted to hold it in place. Be sure you place the lower half correctly: with the "smiley" hole and the cleat-screws closer to the sled.
5. Use 4 M8x35mm bolts and M8 square nuts to secure the lower half of the clamp. It can be a bit tricky to place the nuts, hold the router, and screw things together. It's a bit easier if you flip the whole rig on its back on a table.
6. It's not horribly important that you have your router precisely facing the hose opening, but get it as close to that as possible. If you mount it wrong, the power cord and back part of the router can make contact with the axis cap and cause runtime issues.
7. Don't tighten the M8 bolts right away, just make them snug at first. Then check the router's placement and orientation and tighten things down.
8. When tightening, alternate between the left-side and right-side bolts, using small (e.g. 1/4 turn) turns. This makes sure you don't stress one side of the clamp too much.
9. Here's where you find out if you printed the router clamp with enough infill. Less than 50% infill and it's liable to crack when you try to tighten it down fully.

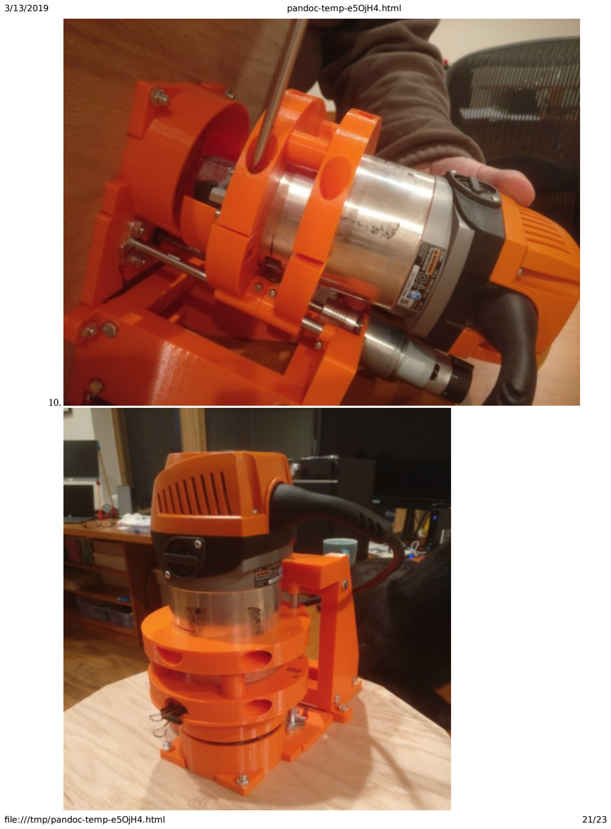
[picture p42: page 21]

10.

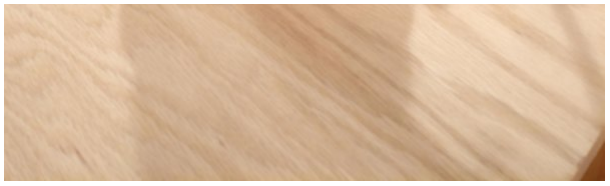
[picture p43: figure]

### Pre-flight and Usage

0. Before attempting any moves in GC, be sure to modify your GC configuration. Find the setting for Z-axis pitch, and put the appropriate setting for your lead screw. If you bought the kit I linked in the BOM, that value should be 8mm.
0. NOTE that this kit does not have an end-stop, so you can tell GC to crash the nut into the coupler or the pillow-block at bottom. Be cautious in your moves, and be ready to hit the "Stop!" button in GC if you've mistakenly told GC to lower / raise beyond the limits.
1. Test your kit by moving your new z axis up and down (in small increments at first).
2. Prior to actually doing any cutting, be sure to define "zero" on your newly-installed Z axis kit.
1. The dust sleeve is designed to go on and come off easily so you can access the collet and change bits. To place it initially:
0. Slide the back into the cleating screws you placed in the bottom of the body clamp:


1.
2. Once the sleeve is fully engaged on the cleating screws, place a medium-size binder clip at the front clip-point (the smiley-shaped opening):


3.
2. To access your collet and change bits and zero your router:
0. Remove the binder clip and remove the front part of the dust sleeve
1. Raise your router to maximum height so it clears the dust shroud
2. You should be able to access the collet lock from behind, and get a wrench into the opening where the dust sleeve had been.

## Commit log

2018-10-20 init commit
    [Router_clamp_both.stl, Router_clamp_lower.stl, Router_clamp_upper.stl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]
2019-04-14 Add files via upload
    Adding revised and new individual file for fine-grained control over what you print.
    [v3_body_clamp_back_half_bottom_only.stl, v3_body_clamp_back_half_top_only.stl, v3_body_clamp_front_half_braced_pair_bottom_only.stl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]
2020-10-26 Add files via upload
    Alternate version of v3_rods_base.stl. Use if your hardware (pillow-block and linear-rod feet) is too chonky to fit in the original base.
    [v3_rods_base_alternate(for larger pillow-block).stl]
